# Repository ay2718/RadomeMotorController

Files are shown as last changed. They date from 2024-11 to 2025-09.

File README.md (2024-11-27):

# Radome motor controller

## CAN protocol

The Radome CAN protocol is very simple.  Send azimuth commands to address 0x1 and elevation commands to address 0x2.  Azimuth and elevation reply back from addresses 0x101 and 0x102 respectively.  Any packet sent to address 0x0 will trigger both azimuth and elevation to reply back with their current status without initiating a motor movement, sending commands will also trigger a reply back.

Even if you feed the CAN total garbage the dish will not exceed safe positions (for elevation), speeds, or acceleration.

The controllers must be updated at least every 100 ms or faster. Othewise they will safely bring the dish to a halt.

The command structure is as follows:

```
Transmit:
// 2^24 is 360 degrees, position is unsigned
tx byte 0 = position bits 23:16
tx byte 1 = position bits 15:8
tx byte 2 = position bits 7:0

// LSB is 1 arcsecond/s = 1/1200 dps, signed
tx byte 3 = velocity bits 15:8
tx byte 4 = velocity bits 7:0

Receive:
// 2^24 is 360 degrees, position is unsigned
rx byte 0 = position bits 23:16
rx byte 1 = position bits 15:8
rx byte 2 = position bits 7:0

// LSB is 1 arcsecond/s = 1/1200 dps, signed
rx byte 3 = velocity bits 15:8
rx byte 4 = velocity bits 7:0

// LSB is 1 mA, signed
rx byte 5 = current bits 15:8
rx byte 6 = current bits 7:0

// LSB is 0.5V, unsigned
rx byte 7 = bus voltage bits 7:0
```

I recommend casting position as a `uint32_t` such that 2<sup>32</sup> is equivalent to 360 degrees.  This makes position math very nice since overflow lines up with one rotation.

We feed the dish position *and* velocity because the velocity information in order to generate very smooth trajectories.  If you want to command a position and you don't care much about timing, it's fine to send a position command with zero velocity.  If you're tracking a satellite moving a couple degrees per second across the sky on X band, the velocity really helps (empirically we were able to maintain 0.05 degrees of tracking error up to 10 dps or so)

## Firmware overview

If you decide to build the firmware, this is an STM32CubeIDE project.  You may need to enable floating point support for printf.  Define or underine azimuth or elevation in Core/Inc/main.h to set azimuth or elevation.  Encoder offsets are hardcoded in.

## CAN Bootloader usage

`az_bootloader.bin` and `el_bootloader.bin` should already be loaded onto their respective motor drives.  The bootloader takes up 2 flash pages on each drive (4 kB)

`flash_motor.py` is used to upload firmware over CAN bus.  The baud rate is 125000 (same as for operating the drives).

Example usage: `./flash_motor.py` --id 0x01  -f radome_azimuth.bin`.
The `--id` flag selects which drive to write toe (0x01 is azimuth, 0x02 is elevation) and the `-f` or `--filename` flag selects the binfile to upload.

If a motor drive is unresponsive to being flashed, try running `./flash_motor.py ...`, leave it running, and cycle power to the motor drives.  This is useful if there's a problem with the firmware--`flash_motor.py` sends out pings to each motor's address every 100ms and the drives wait for pings in bootloader mode for 500ms before starting up.

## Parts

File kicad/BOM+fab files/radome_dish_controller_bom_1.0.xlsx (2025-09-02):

Component | Description | Part | References | Value | Footprint | Quantity Per PCB | Datasheet | LCSC | digikeypn | P/N
1 | Unpolarized capacitor | C | ANACAP201 | 10nF | C_0603_1608Metric | 1 | ~ | C1589 | 1276-1009-1-ND
2 | Unpolarized capacitor | C | C113 C114 C201 C202 C203 C204 C205 C206 C304 C305 C306 C308 C309 C312 C313 | 100nF | C_0603_1608Metric | 15 | ~ | C1591 | 1276-1935-1-ND
3 | Unpolarized capacitor | C | C102 C103 C105 C106 C108 C109 | 10uF | C_2220_5650Metric | 6 | ~ | C153035
4 | Unpolarized capacitor | C | C107 C110 C111 C112 | 10uF | C_1206_3216Metric | 4 | ~ | C13585
5 | Unpolarized capacitor | C | C301 C302 C303 C307 C310 C311 | 1uF | C_0603_1608Metric | 6 | ~ | C15849 | 1276-1860-1-ND
6 | Polarized capacitor, US symbol | C_Polarized_US | C101 C104 | 220uF | CP_Radial_D12.5mm_P5.00mm | 2 | ~
7 | 75V 0.15A Fast Switching Diode, SOD-123 | 1N4148W | D301 D302 D303 | 1N4148W | D_SOD-123 | 3 | https://www.vishay.com/docs/85748/1n4148w.pdf | C112342 | 1N4148W-13FDICT-ND
8 | Ferrite bead | FerriteBead | FB201 | 600ohm@100MHz | L_0603_1608Metric | 1 | ~ | C20345 | 732-1593-1-ND
9 | Generic connector, double row, 02x07, odd/even pin numbering scheme (row 1 odd numbers, row 2 even numbers), script generated (kicad-library-utils/schlib/autogen/connector/) | Conn_02x07_Odd_Even | J201 | Conn_02x07_Odd_Even | PinHeader_2x07_P1.27mm_Vertical_SMD | 1 | ~ | C5445007 | 1175-1736-ND
10 | Generic connector, double row, 02x03, top/bottom pin numbering scheme (row 1: 1...pins_per_row, row2: pins_per_row+1 ... num_pins), script generated (kicad-library-utils/schlib/autogen/connector/) | Conn_02x03_Top_Bottom | J106 | Molex Micro-Fit+ | MOLEX_2068320602 | 1 | ~
11 | Generic connector, single row, 01x02, script generated (kicad-library-utils/schlib/autogen/connector/) | Conn_01x02 | J107 J108 | Molex Micro-Fit+ | MOLEX_2165711002 | 2 | ~
12 | Generic screw terminal, single row, 01x01, script generated (kicad-library-utils/schlib/autogen/connector/) | Screw_Terminal_01x01 | J101 J102 J103 J104 J105 | Solder Pad | SolderWirePad_1x01_SMD_5x10mm | 5 | ~
13 | Inductor | L | L101 | 2.2uH | L_Vishay_IHLP-5050 | 1 | https://www.vishay.com/docs/34337/ihlp5050fd5a.pdf | C845090 |  | IHLP5050FDER2R2M5A
14 | 30A Id, 30V Vds, 2.4mOhm Ron, PowerPAK-8 | Si7336ADP | Q301 Q302 Q303 Q304 Q305 Q306 | SIR680DP-T1-RE3 | PowerPAK_SO-8_Single | 6 | https://www.vishay.com/docs/65162/sir426dp.pdf |  | SIR426DP-T1-GE3CT-ND
15 | Resistor | R | R101 | 1 | R_2512_6332Metric | 1 | ~ | C11254
16 | Resistor | R | R204 | 100k | R_0603_1608Metric | 1 | ~ | C25803
17 | Resistor | R | R313 | 10k | R_0603_1608Metric | 1 | ~ | C859110 | RMCF0603FT10K0CT-ND
18 | Resistor | R | R310 R311 | 1k | R_0603_1608Metric | 2 | ~ | C2924142 | RMCF0603FT10K0CT-ND
19 | Shunt resistor | R_Shunt | R307 R308 R309 | 1m | R_Shunt_Vishay_WSK2512_6332Metric_T2.21mm | 3 | ~ | C459678
20 | Resistor | R | R312 | 200k | R_0603_1608Metric | 1 | ~ | C25811 | CR0603-FX-5102ELFCT-ND
21 | Resistor | R | R301 R302 R303 R304 R305 R306 | 3 | R_0603_1608Metric | 6 | ~ | C137724 | RMCF0603FT3R00CT-ND
22 | On-Axis Magnetic Position Sensor, 14-bit, PWM Output, ABI Output, UVW Output, SPI Interface, TSSOP-14 | AS5047D | U101 | AS5047D | TSSOP-14_4.4x5mm_P0.65mm | 1 | https://ams.com/documents/20143/36005/AS5047D_DS000394_2-00.pdf | C962063
23 | 1A 20V Fixed LDO Linear Regulator, 3.3V, SOT-89/SOT-223/TO-220/TO-252/TO-263 | AZ1117-3.3 | U104 | AZ1117-3.3 | SOT-223-3_TabPin2 | 1 | https://www.diodes.com/assets/Datasheets/AZ1117.pdf | C435835
24 | 1A 20V Fixed LDO Linear Regulator, 5.0V, SOT-89/SOT-223/TO-220/TO-252/TO-263 | AZ1117-5.0 | U105 | AZ1117-5.0 | SOT-223-3_TabPin2 | 1 | https://www.diodes.com/assets/Datasheets/AZ1117.pdf | C526405
25 | Bidirectional, Low- and High-Side Voltage Output, Current-Sense Amplifier, SOT-23-6 | INA181 | U304 U305 U306 | INA181-A2 | SOT-23-6 | 3 | http://www.ti.com/lit/ds/symlink/ina181.pdf | C116200 | 296-47657-1-ND
26 | DC/DC buck converter | K78UXX | U106 | K78UXX | K78UXX-RightAngle | 1 | https://www.mornsun-power.com/html/pdf/K78U12-500R3L.html
27 | High and Low Side Driver, 600V, 1.4/1.8A, PDIP-8/SOIC-8 | IRS2181 | U301 U302 U303 | LF2190N | SOIC-8_3.9x4.9mm_P1.27mm | 3 | https://www.littelfuse.com/~/media/electronics/datasheets/power_semiconductors/littelfuse_gate_drivers_lf2190n_datasheet.pdf.pdf | C3655431 | 212-LF2190NTRCT-ND
28 | High-Speed CAN Transceiver, 1Mbps, 3.3V supply | MAX3051 | U202 | MAX3051 | SO-8_3.9x4.9mm_P1.27mm | 1 | http://datasheets.maximintegrated.com/en/ds/MAX3051.pdf | C15648
29 | Differential RS-422/RS-485 bus transceiver, SOIC-8 | SN75176AD | U102 U103 | SN75176AD | SOIC-8_3.9x4.9mm_P1.27mm | 2 | http://www.ti.com/lit/ds/symlink/sn75176a.pdf | C468242
30 |  | STM32G431CBU3_1 | U201 | STM32G431CBU3 | QFN-48-1EP_7x7mm_P0.5mm_EP5.3x5.3mm | 1 |  | C529356 | STM32G431CBU3-ND
31 | Three pin crystal, GND on pin 2 | Crystal_GND2 | Y201 | 16MHz | Resonator_SMD_Murata_CSTxExxV-3Pin_3.0x1.1mm | 1 | ~ | C341521 | 490-17948-1-ND
Component Groups: | 31
Component Count: | 84
Fitted Components: | 84
Number of PCBs: | 1
Total components: | 84
Schematic Version: | 1.0
Schematic Date: | 2023-03-29
BoM Date: | Sat 01 Jul 2023 03:16:00 PM EDT
Schematic Source: | radome_dish_controller.kicad_sch
KiCad Version: | Eeschema 7.0.5-1.fc38

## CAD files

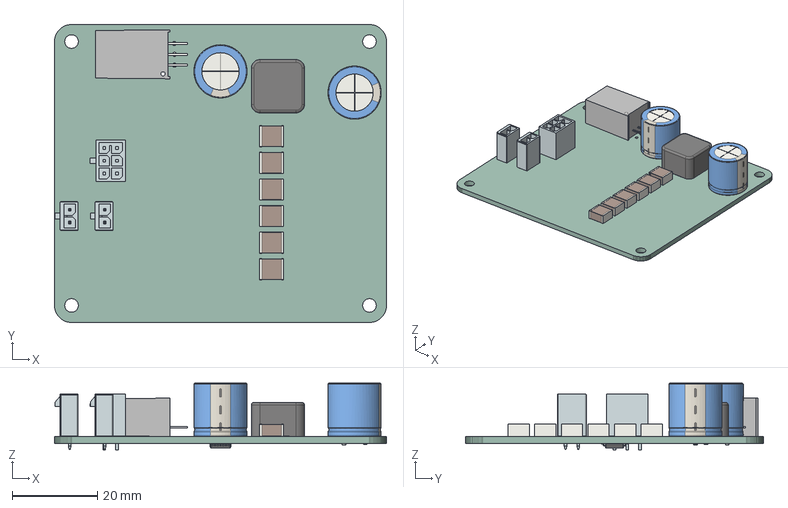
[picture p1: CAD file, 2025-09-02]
kicad/radome_dish_controller.step
78.0 x 70.0 x 15.6 mm
radome_dish_controller PCB

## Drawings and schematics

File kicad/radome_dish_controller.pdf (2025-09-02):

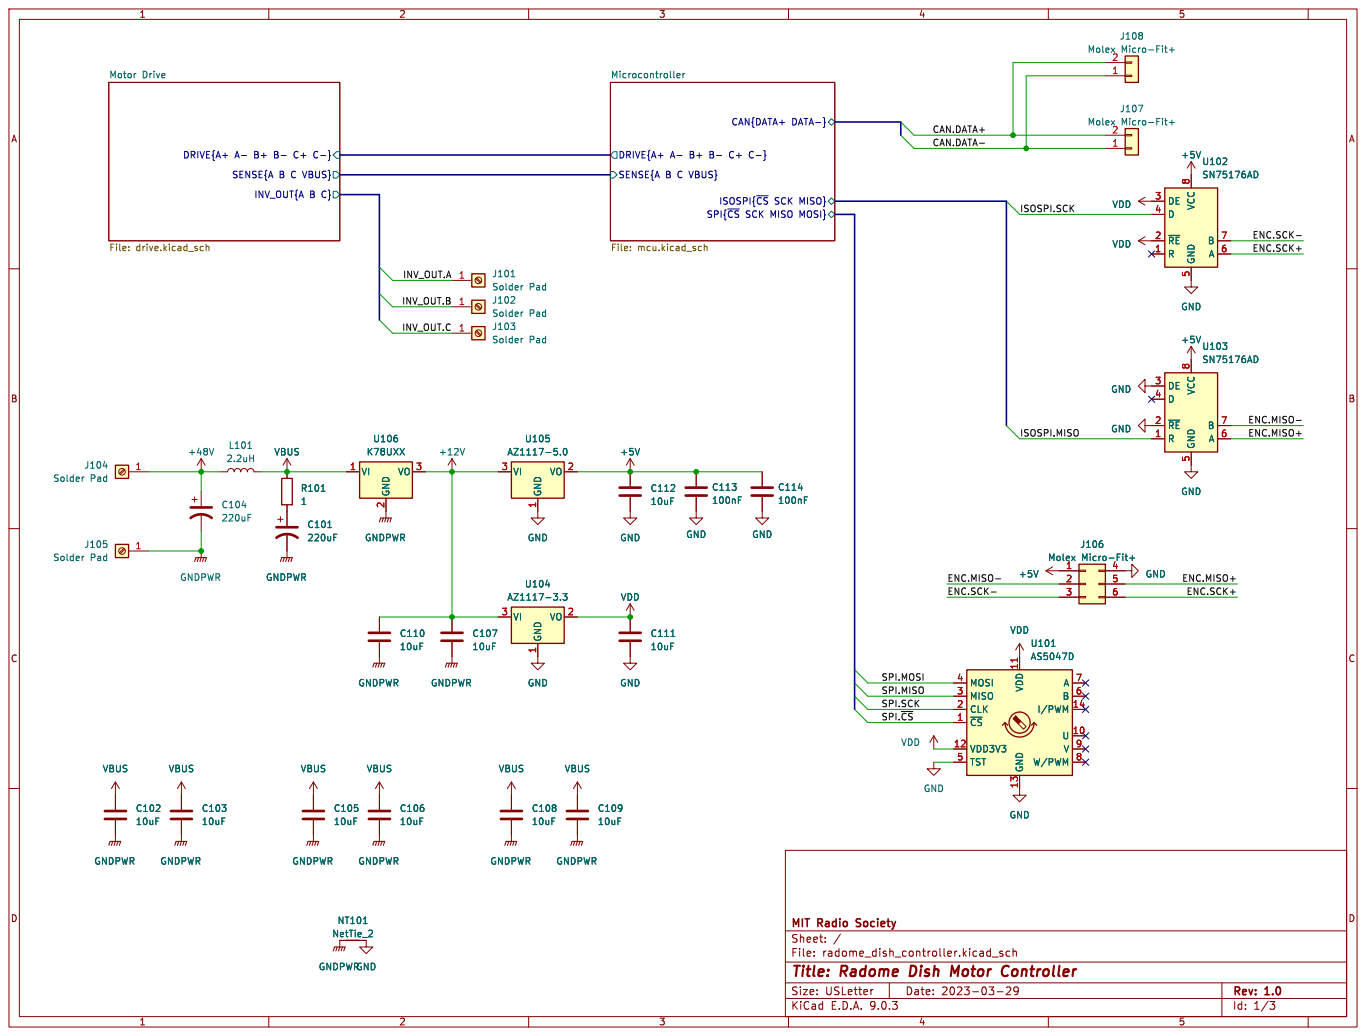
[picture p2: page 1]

SPI{~{CS}SCK MISO MOSI} Microcontroller File: mcu.kicad_sch DRIVE{A+ A- B+ B- C+ C-}

J107 Molex Micro-Fit+ GNDPWR GNDPWR

ISOSPI{~{CS}SCK MISO}

ENC.SCK- SPI.~{CS}

ENC.SCK- ENC.MISO-

SPI.MOSI SPI.MISO

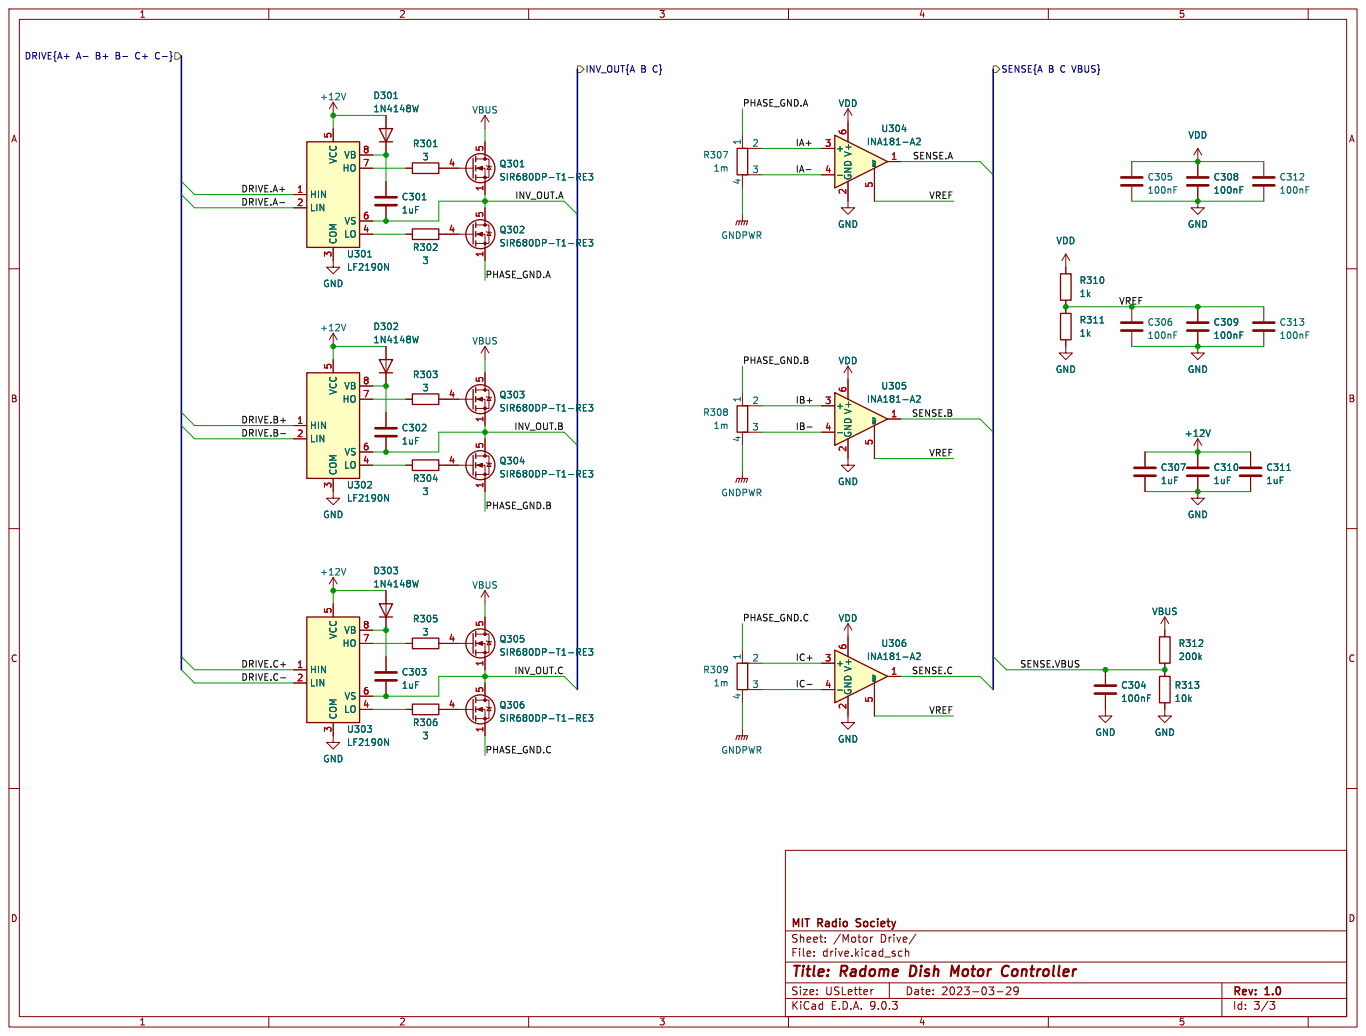
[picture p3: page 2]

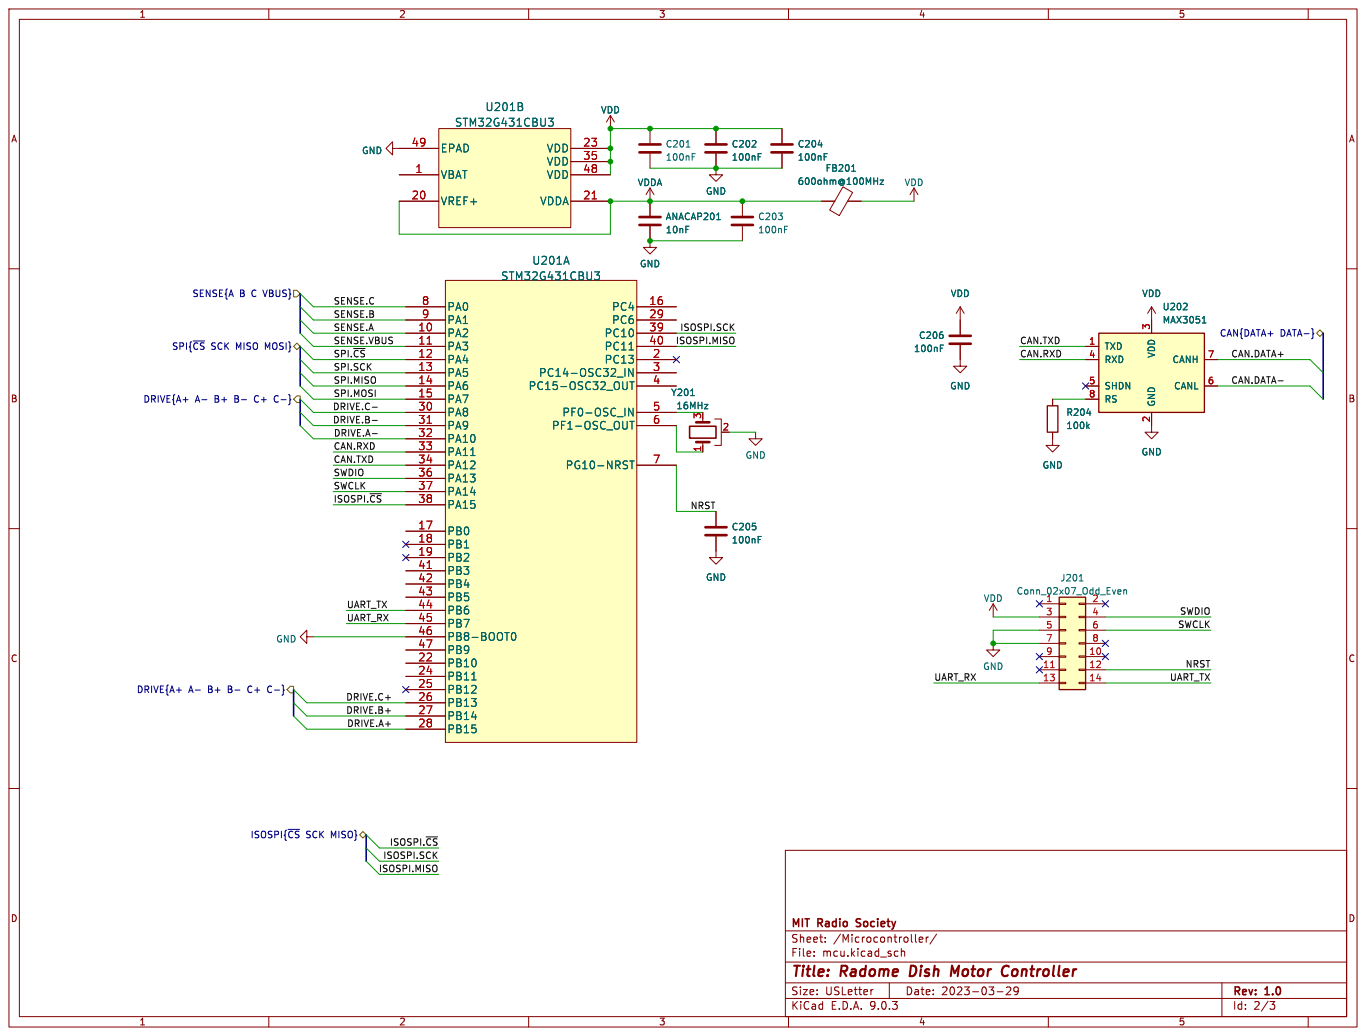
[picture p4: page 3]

SPI.~{CS} SPI.SCK DRIVE.C- DRIVE.B- SENSE.A
SENSE.VBUS

SPI{~{CS}SCK MISO MOSI}

SPI.MOSI SPI.MISO

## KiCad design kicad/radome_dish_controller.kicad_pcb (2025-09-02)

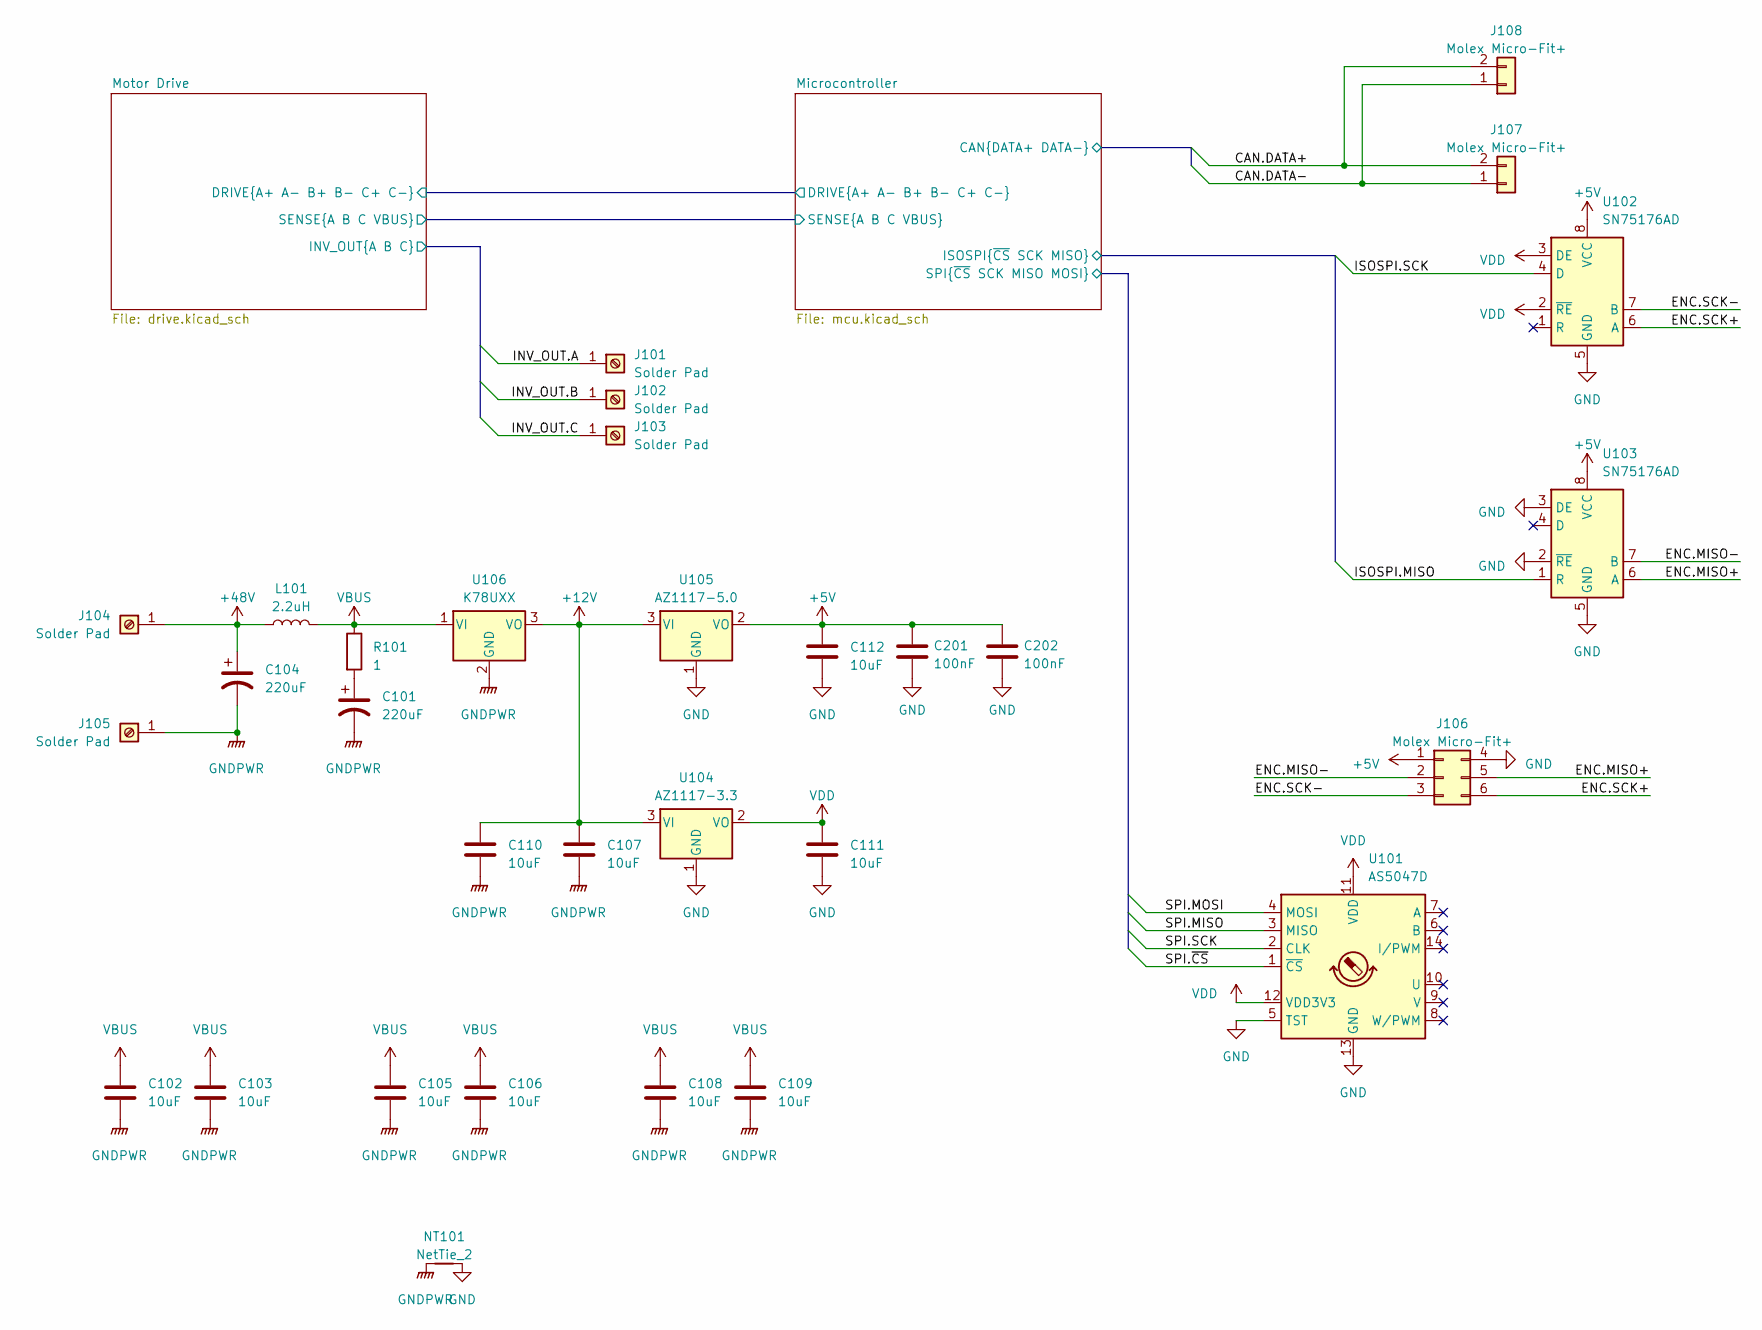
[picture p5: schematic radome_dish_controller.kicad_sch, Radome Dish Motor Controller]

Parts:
C101, C104: 220uF; CP_Radial_D12.5mm_P5.00mm
C102, C103, C105, C106, C108, C109: 10uF; C_2220_5650Metric; LCSC C153035
C107, C110, C111, C112: 10uF; C_1206_3216Metric; LCSC C13585
C201, C202: 100nF; C_0603_1608Metric; digikeypn 1276-1935-1-ND
J101, J102, J103, J104, J105: Solder Pad; SolderWirePad_1x01_SMD_5x10mm
J106: Molex Micro-Fit+; MOLEX_2068320602
J107, J108: Molex Micro-Fit+; MOLEX_2165711002
L101: 2.2uH; L_Vishay_IHLP-5050; LCSC C845090
NT101: NetTie_2; NetTie-2_SMD_Pad2.0mm
R101: 1; R_2512_6332Metric; LCSC C11254
U101: AS5047D; TSSOP-14_4.4x5mm_P0.65mm; LCSC C962063
U102, U103: SN75176AD; SOIC-8_3.9x4.9mm_P1.27mm; LCSC C468242
U104: AZ1117-3.3; SOT-223-3_TabPin2; LCSC C435835
U105: AZ1117-5.0; SOT-223-3_TabPin2; LCSC C526405
U106: K78UXX; K78UXX-RightAngle

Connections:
+12V: C107.1, C110.1, U104.3 (VI), U105.3 (VI), U106.3 (VO); also elsewhere on the board
+48V: C104.1, J104.1, L101.1
/ENC.MISO+: J106.5, U103.6 (A)
/ENC.MISO-: J106.2, U103.7 (B)
/ENC.SCK+: J106.6, U102.6 (A)
/ENC.SCK-: J106.3, U102.7 (B)
/Microcontroller/CAN.DATA+: J107.2, J108.2; also elsewhere on the board
/Microcontroller/CAN.DATA-: J107.1, J108.1; also elsewhere on the board
/Microcontroller/ISOSPI.MISO: U103.1 (R); also elsewhere on the board
/Microcontroller/ISOSPI.SCK: U102.4 (D); also elsewhere on the board
/Microcontroller/SPI.MISO: U101.3 (MISO); also elsewhere on the board
/Microcontroller/SPI.MOSI: U101.4 (MOSI); also elsewhere on the board
/Microcontroller/SPI.SCK: U101.2 (CLK); also elsewhere on the board
/Microcontroller/SPI.~CS: U101.1 (~CS); also elsewhere on the board
/Motor Drive/INV_OUT.A: J101.1; also elsewhere on the board
/Motor Drive/INV_OUT.B: J102.1; also elsewhere on the board
/Motor Drive/INV_OUT.C: J103.1; also elsewhere on the board
GND: C111.2, C112.2, C201.2, C202.2, J106.4, NT101.2, U101.5 (TST), U101.13 (GND), U102.5 (GND), U103.2 (~RE), U103.3 (DE), U103.5 (GND), U104.1 (GND), U105.1 (GND); also elsewhere on the board
GNDPWR: C101.2, C102.2, C103.2, C104.2, C105.2, C106.2, C107.2, C108.2, C109.2, C110.2, J105.1, NT101.1, U106.2 (GND); also elsewhere on the board
unnamed: C101.1, R101.2
VBUS: C102.1, C103.1, C105.1, C106.1, C108.1, C109.1, L101.2, R101.1, U106.1 (VI); also elsewhere on the board

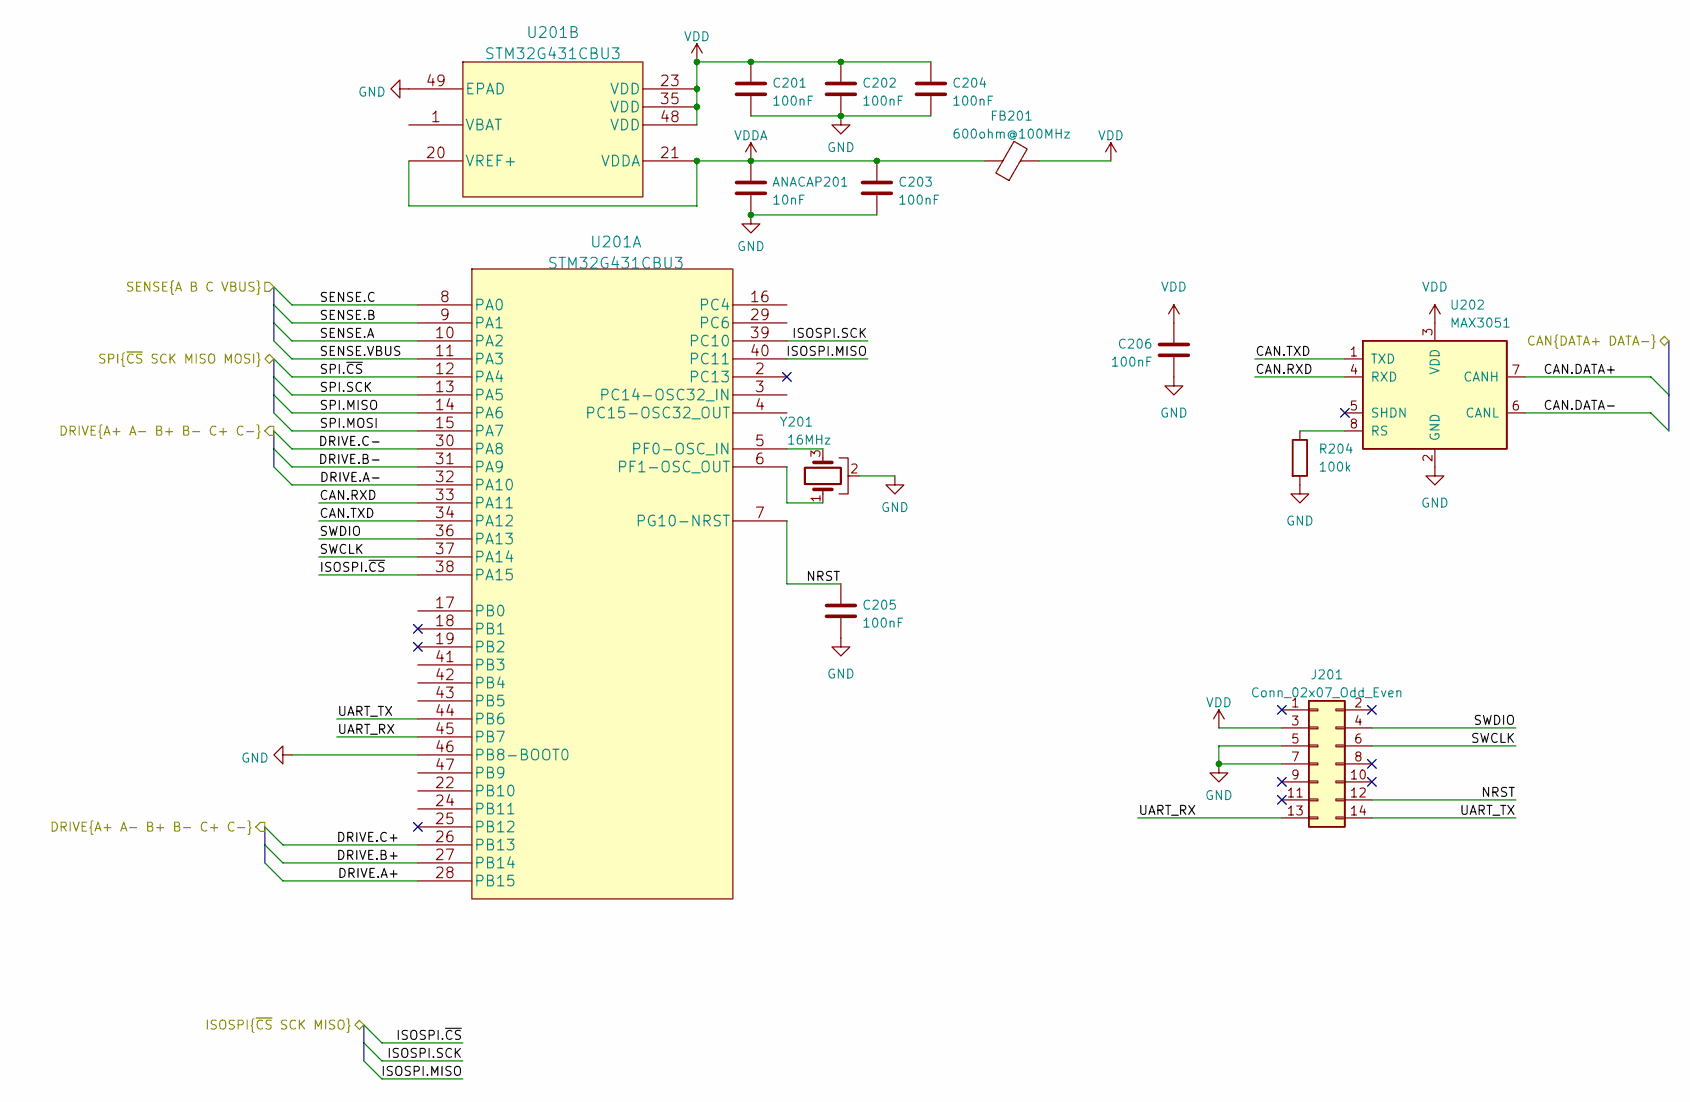
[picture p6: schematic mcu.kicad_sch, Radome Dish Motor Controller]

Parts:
ANACAP201: 10nF; C_0603_1608Metric; digikeypn 1276-1009-1-ND
C201, C202, C203, C204, C205, C206: 100nF; C_0603_1608Metric; digikeypn 1276-1935-1-ND
FB201: 600ohm@100MHz; L_0603_1608Metric; digikeypn 732-1593-1-ND
J201: Conn_02x07_Odd_Even; PinHeader_2x07_P1.27mm_Vertical_SMD; digikeypn 1175-1736-ND
R204: 100k; R_0603_1608Metric; LCSC C25803
U201: STM32G431CBU3; QFN-48-1EP_7x7mm_P0.5mm_EP5.3x5.3mm; digikeypn STM32G431CBU3-ND
U202: MAX3051; SO-8_3.9x4.9mm_P1.27mm; LCSC C15648
Y201: 16MHz; Resonator_SMD_Murata_CSTxExxV-3Pin_3.0x1.1mm; digikeypn 490-17948-1-ND

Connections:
/Microcontroller/CAN.DATA+: U202.7 (CANH); also elsewhere on the board
/Microcontroller/CAN.DATA-: U202.6 (CANL); also elsewhere on the board
/Microcontroller/CAN.RXD: U201.33 (PA11), U202.4 (RXD)
/Microcontroller/CAN.TXD: U201.34 (PA12), U202.1 (TXD)
/Microcontroller/DRIVE.A+: U201.28 (PB15); also elsewhere on the board
/Microcontroller/DRIVE.A-: U201.32 (PA10); also elsewhere on the board
/Microcontroller/DRIVE.B+: U201.27 (PB14); also elsewhere on the board
/Microcontroller/DRIVE.B-: U201.31 (PA9); also elsewhere on the board
/Microcontroller/DRIVE.C+: U201.26 (PB13); also elsewhere on the board
/Microcontroller/DRIVE.C-: U201.30 (PA8); also elsewhere on the board
/Microcontroller/ISOSPI.MISO: U201.40 (PC11); also elsewhere on the board
/Microcontroller/ISOSPI.SCK: U201.39 (PC10); also elsewhere on the board
/Microcontroller/ISOSPI.~CS: U201.38 (PA15)
/Microcontroller/NRST: C205.1, J201.12, U201.7 (PG10-NRST)
/Microcontroller/SENSE.A: U201.10 (PA2); also elsewhere on the board
/Microcontroller/SENSE.B: U201.9 (PA1); also elsewhere on the board
/Microcontroller/SENSE.C: U201.8 (PA0); also elsewhere on the board
/Microcontroller/SENSE.VBUS: U201.11 (PA3); also elsewhere on the board
/Microcontroller/SPI.MISO: U201.14 (PA6); also elsewhere on the board
/Microcontroller/SPI.MOSI: U201.15 (PA7); also elsewhere on the board
/Microcontroller/SPI.SCK: U201.13 (PA5); also elsewhere on the board
/Microcontroller/SPI.~CS: U201.12 (PA4); also elsewhere on the board
/Microcontroller/SWCLK: J201.6, U201.37 (PA14)
/Microcontroller/SWDIO: J201.4, U201.36 (PA13)
/Microcontroller/UART_RX: J201.13, U201.45 (PB7)
/Microcontroller/UART_TX: J201.14, U201.44 (PB6)
GND: ANACAP201.2, C201.2, C202.2, C203.2, C204.2, C205.2, C206.2, J201.5, J201.7, R204.2, U201.46 (PB8-BOOT0), U201.49 (EPAD), U202.2 (GND), Y201.2; also elsewhere on the board
unnamed: U201.5 (PF0-OSC_IN), Y201.3
unnamed: U201.6 (PF1-OSC_OUT), Y201.1
unnamed: R204.1, U202.8 (RS)
VDDA: ANACAP201.1, C203.1, FB201.1, U201.20 (VREF+), U201.21 (VDDA)

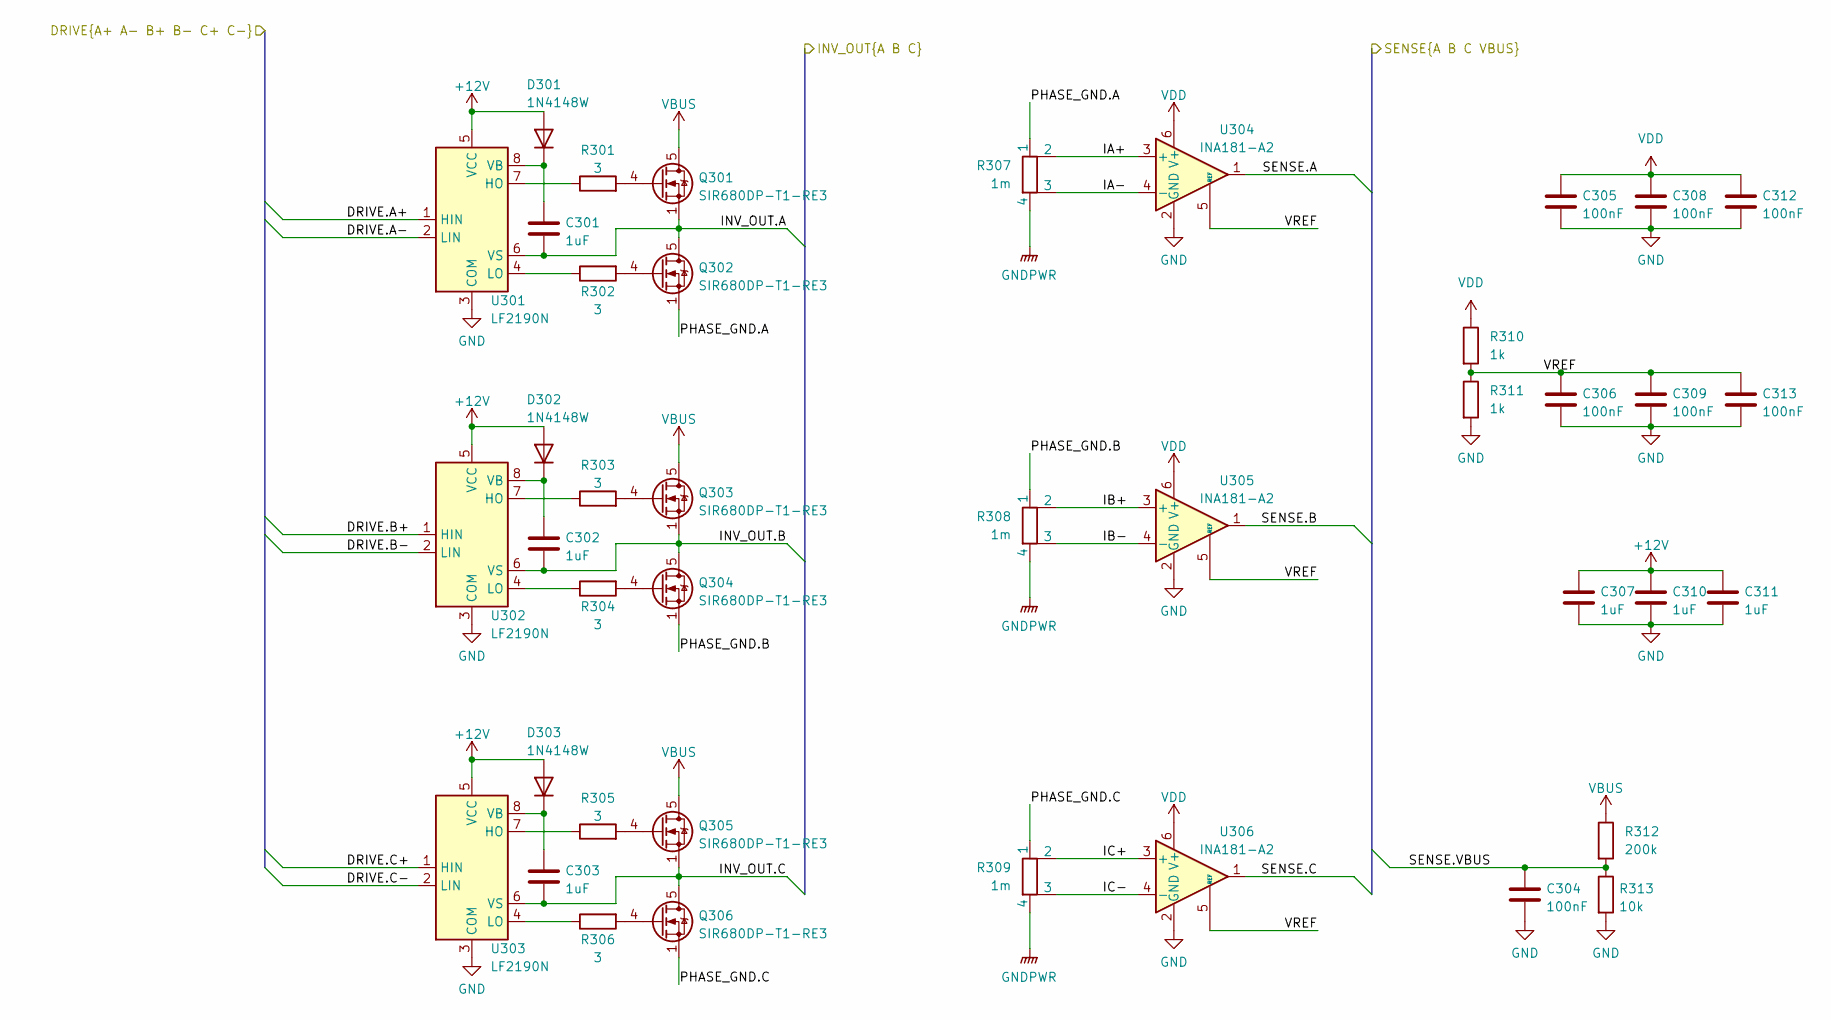
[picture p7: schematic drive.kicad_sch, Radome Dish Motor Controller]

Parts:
C301, C302, C303, C307, C310, C311: 1uF; C_0603_1608Metric; digikeypn 1276-1860-1-ND
C304, C305, C306, C308, C309, C312, C313: 100nF; C_0603_1608Metric; digikeypn 1276-1935-1-ND
D301, D302, D303: 1N4148W; D_SOD-123; digikeypn 1N4148W-13FDICT-ND
Q301, Q302, Q303, Q304, Q305, Q306: SIR680DP-T1-RE3; PowerPAK_SO-8_Single; digikeypn SIR426DP-T1-GE3CT-ND
R301, R302, R303, R304, R305, R306: 3; R_0603_1608Metric; digikeypn RMCF0603FT3R00CT-ND
R307, R308, R309: 1m; R_Shunt_Vishay_WSK2512_6332Metric_T2.21mm; LCSC C459678
R310, R311: 1k; R_0603_1608Metric; digikeypn RMCF0603FT10K0CT-ND
R312: 200k; R_0603_1608Metric; digikeypn CR0603-FX-5102ELFCT-ND
R313: 10k; R_0603_1608Metric; digikeypn RMCF0603FT10K0CT-ND
U301, U302, U303: LF2190N; SOIC-8_3.9x4.9mm_P1.27mm; digikeypn 212-LF2190NTRCT-ND
U304, U305, U306: INA181-A2; SOT-23-6; digikeypn 296-47657-1-ND

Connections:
+12V: C307.1, C310.1, C311.1, D301.2 (A), D302.2 (A), D303.2 (A), U301.5 (VCC), U302.5 (VCC), U303.5 (VCC); also elsewhere on the board
/Microcontroller/DRIVE.A+: U301.1 (HIN); also elsewhere on the board
/Microcontroller/DRIVE.A-: U301.2 (LIN); also elsewhere on the board
/Microcontroller/DRIVE.B+: U302.1 (HIN); also elsewhere on the board
/Microcontroller/DRIVE.B-: U302.2 (LIN); also elsewhere on the board
/Microcontroller/DRIVE.C+: U303.1 (HIN); also elsewhere on the board
/Microcontroller/DRIVE.C-: U303.2 (LIN); also elsewhere on the board
/Microcontroller/SENSE.A: U304.1; also elsewhere on the board
/Microcontroller/SENSE.B: U305.1; also elsewhere on the board
/Microcontroller/SENSE.C: U306.1; also elsewhere on the board
/Microcontroller/SENSE.VBUS: C304.1, R312.2, R313.1; also elsewhere on the board
/Motor Drive/IA+: R307.2, U304.3 (+)
/Motor Drive/IA-: R307.3, U304.4 (-)
/Motor Drive/IB+: R308.2, U305.3 (+)
/Motor Drive/IB-: R308.3, U305.4 (-)
/Motor Drive/IC+: R309.2, U306.3 (+)
/Motor Drive/IC-: R309.3, U306.4 (-)
/Motor Drive/INV_OUT.A: C301.2, Q301.1 (S), Q301.2 (S), Q301.3 (S), Q302.5 (D), U301.6 (VS); also elsewhere on the board
/Motor Drive/INV_OUT.B: C302.2, Q303.1 (S), Q303.2 (S), Q303.3 (S), Q304.5 (D), U302.6 (VS); also elsewhere on the board
/Motor Drive/INV_OUT.C: C303.2, Q305.1 (S), Q305.2 (S), Q305.3 (S), Q306.5 (D), U303.6 (VS); also elsewhere on the board
/Motor Drive/PHASE_GND.A: Q302.1 (S), Q302.2 (S), Q302.3 (S), R307.1
/Motor Drive/PHASE_GND.B: Q304.1 (S), Q304.2 (S), Q304.3 (S), R308.1
/Motor Drive/PHASE_GND.C: Q306.1 (S), Q306.2 (S), Q306.3 (S), R309.1
/Motor Drive/VREF: C306.1, C309.1, C313.1, R310.2, R311.1, U304.5 (REF), U305.5 (REF), U306.5 (REF)
GND: C304.2, C305.2, C306.2, C307.2, C308.2, C309.2, C310.2, C311.2, C312.2, C313.2, R311.2, R313.2, U301.3 (COM), U302.3 (COM), U303.3 (COM), U304.2 (GND), U305.2 (GND), U306.2 (GND); also elsewhere on the board
GNDPWR: R307.4, R308.4, R309.4; also elsewhere on the board
unnamed: C301.1, D301.1 (K), U301.8 (VB)
unnamed: C302.1, D302.1 (K), U302.8 (VB)
unnamed: C303.1, D303.1 (K), U303.8 (VB)
unnamed: Q301.4 (G), R301.2
unnamed: Q302.4 (G), R302.2
unnamed: Q303.4 (G), R303.2
unnamed: Q304.4 (G), R304.2
unnamed: Q305.4 (G), R305.2
unnamed: Q306.4 (G), R306.2
unnamed: R301.1, U301.7 (HO)
unnamed: R302.1, U301.4 (LO)
unnamed: R303.1, U302.7 (HO)
unnamed: R304.1, U302.4 (LO)
unnamed: R305.1, U303.7 (HO)
unnamed: R306.1, U303.4 (LO)
VBUS: Q301.5 (D), Q303.5 (D), Q305.5 (D), R312.1; also elsewhere on the board

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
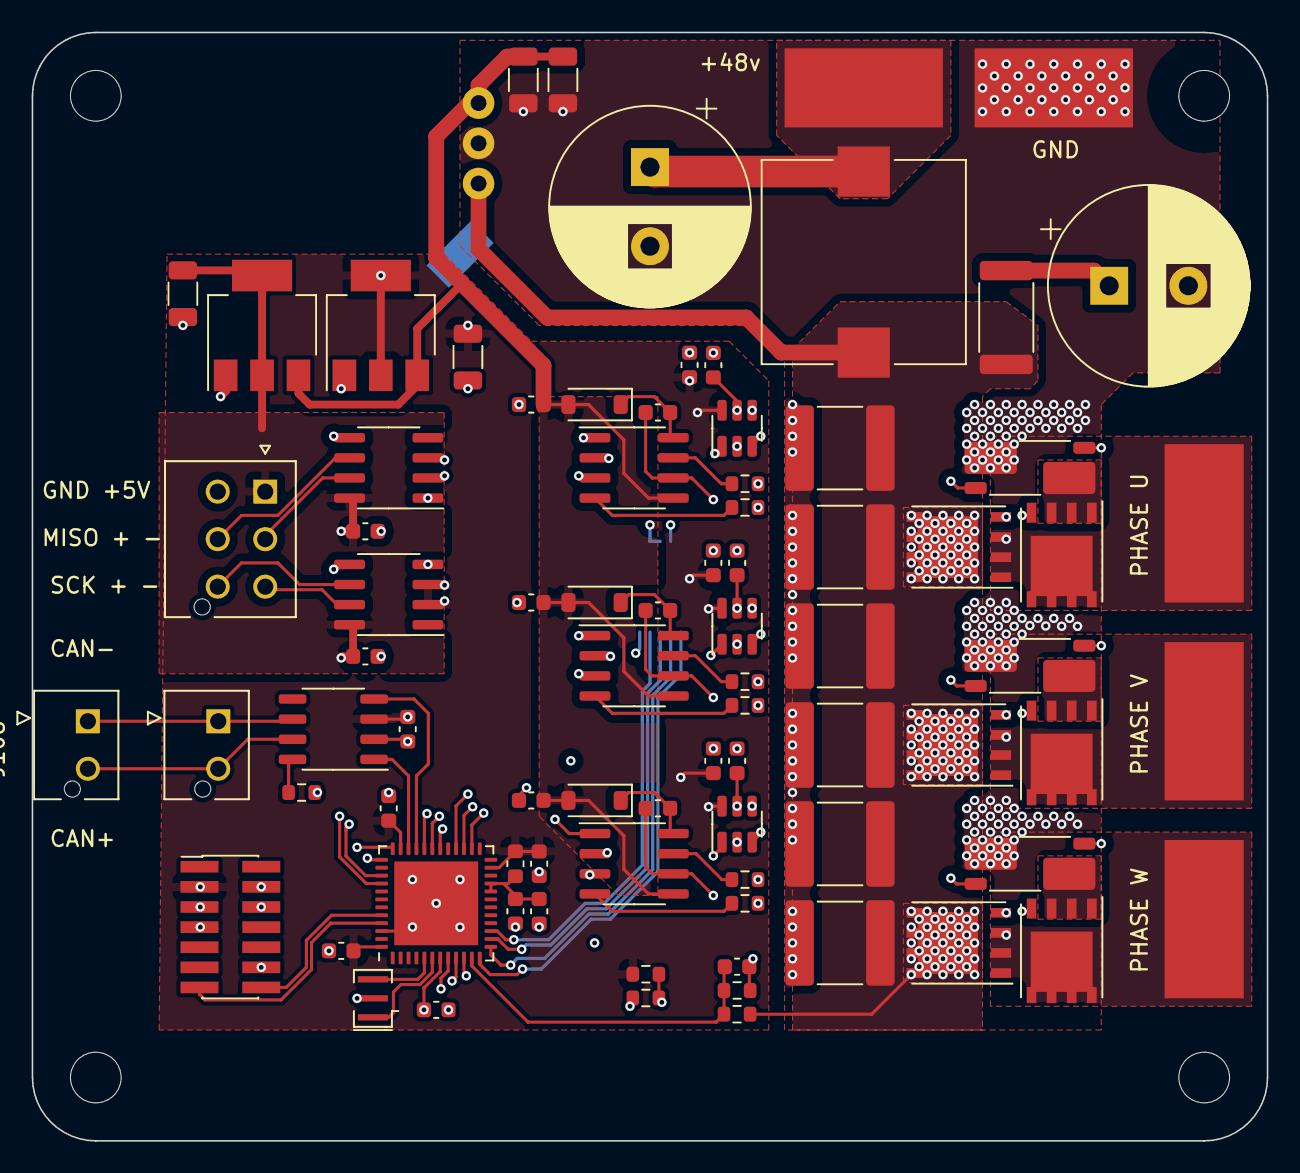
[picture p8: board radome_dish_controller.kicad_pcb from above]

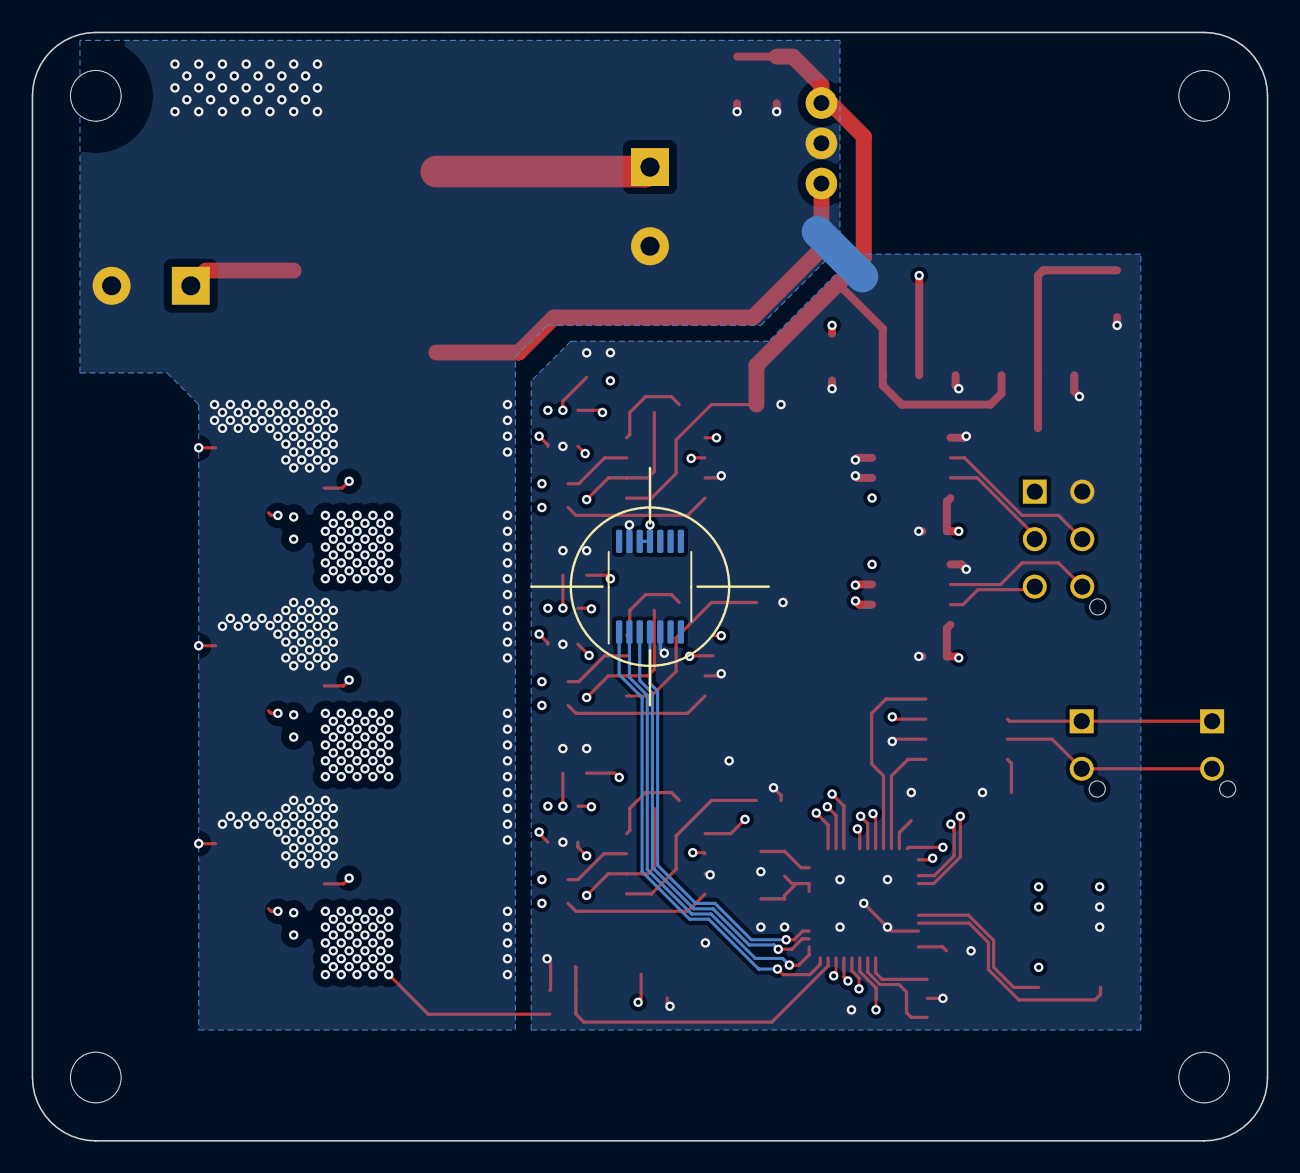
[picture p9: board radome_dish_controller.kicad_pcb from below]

Board: 4 copper layers, 78.0 x 70.0 mm, 85 parts (2 on the bottom side), 69 nets.

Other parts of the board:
C113, C114: 100nF; C_0603_1608Metric

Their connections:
GND: C113.2, C114.2; also elsewhere on the board

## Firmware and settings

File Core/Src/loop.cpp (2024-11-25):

/*
 * control_loop.cpp
 *
 *  Created on: Aug 14, 2022
 *      Author: ayeiser
 */

#include <loop.h>
#include "tim_delay.h"
#include "control.h"
#include "EMFPositionSensor.h"
#include "CurrentSensor.h"
#include "stdio.h"
#include "main.h"
#include "retarget.h"

#include "AS5047PositionSensor.h"
#include "CANHandler.h"
#include "ZettlexIncoder.h"
#include "structs.h"


#define ADC_TO_VOLTAGE (3.3f / 4095.0f)
#define CURRENT_SCALE -(ADC_TO_VOLTAGE / (50.0f * 0.001f)) // 50x shunt gain, 1 mohm shunt
#define VBUS_SCALE (ADC_TO_VOLTAGE * 21.0f) // 200k and 10k divider

#define DELAY_CORR 0.0f

extern TIM_HandleTypeDef htim1, htim6, htim7;
extern ADC_HandleTypeDef hadc1, hadc2;
extern UART_HandleTypeDef huart1;
extern SPI_HandleTypeDef hspi1, hspi3;
extern FDCAN_HandleTypeDef hfdcan1;
extern IWDG_HandleTypeDef hiwdg;

CANHandler canHandler(&hfdcan1);
ZettlexIncoder incoder(&hspi3);

namespace Motor {

#define NUM_POLES 7
const vect_dq Ldq = {250e-6f, 250e-6f};
const float R_phase = 0.3f;

const float dt = 1/float(PWM_FREQ);

ADCReader phaseU(&hadc1, 0, CURRENT_SCALE, 2048);
ADCReader phaseV(&hadc2, 1, CURRENT_SCALE, 2048);
ADCReader phaseW(&hadc2, 0, CURRENT_SCALE, 2048);
ADCReader vbusMeas(&hadc1, 1, VBUS_SCALE, 0);

CurrentSensor current(phaseU, phaseV, phaseW, vbusMeas);
PWMGenerator_WVU pwm(&htim1);
EMFPositionSensor emfpos(current, pwm, dt, NUM_POLES, Ldq, R_phase);
TestPositionSensor fakepos(dt, NUM_POLES);
AS5047PositionSensor as5047pos(&hspi1, dt, NUM_POLES, OFFSET);

LowPassFilter rpmfilter(dt, 100.0f);

CurrentDQController idqc(dt, 10.0f, Ldq, 0.2f);
PIController vel_pi(dt, 0.750f, 0.0f, 0.0f);
//GenericController controller(dt, pos, current, pwm, idqc, DELAY_CORR);

DummyController dummy;
MotorParamFinder params(10.0f);
TorqueController torque(idqc);
//PDVelocityController pdc(idqc, 20.0f);
IncoderPositionController pdc(idqc, incoder, 20.0f);

ParentController* active_controller = &pdc;

motor_command_t motor_command = {
		.position = 0,
		.velocity = 0.0f,
};

motor_reply_t motor_reply = {
		.position = 0,
		.velocity = 0.0f,
		.current = 0.0f,
		.vbus = 0.0f
};

}

const float ParentController::undervoltage_threshold = 15.0f;
const float ParentController::enable_voltage_threshold = 20.0f;
const float ParentController::overvoltage_threshold = 60.0f;
const float ParentController::overcurrent_threshold = 30.0f;

CurrentSensor& ParentController::current = Motor::current;
PWMGenerator& ParentController::pwm = Motor::pwm;
PositionSensor& ParentController::pos = Motor::as5047pos;
//PositionSensor& ParentController::pos = Motor::emfpos;
float ParentController::dt = Motor::dt;

using namespace Motor;


void setup() {
	HAL_Delay(1000);
	RetargetInit(&huart1);
	printf("\n-------------------------------------------------------\n");
	printf(ID_STR "\n");

	printf("Starting CAN...\n");
	canHandler.start();

	printf("Starting ADC reader...\n");
	ADCReader::start();

	printf("Starting htim6...\n");
	start_delay_timer(&htim6);

	printf("Setting up position sensor...\n");
	emfpos.setup();

	as5047pos.setup();

	pdc.setGains(VEL_KP, VEL_KD, PDC_MAX_CURRENT);
	pdc.setPositionGains(0.0f);
	pdc.set_hpf(VEL_HPF);
	pdc.setTargets(as5047pos.getPhaseCorrMechAngle(), 0.0f);
	pdc.setTrajectory(0, 0.0f);


	printf("Setting up PWM generation...\n");
	pwm.startTiming();
	pwm.startSwitching();
	pwm.setAngle(0);
	pwm.update(20.0f);

	HAL_TIM_Base_Start_IT(&htim7);


	printf("Done setup!\n");
}

void loop() {
	// main.c while loop goes here
//	if (active_controller == )

//	if (rxDataReady()) {
//		char c = getchar();
//		printf("c = %c\n", c);
//		if (c == 'x') {
//			ParentController* current = active_controller;
//			active_controller = &params;
//			active_controller->exec();
//			active_controller = current;
//		}
//		if (c == 't') {
//			active_controller = &torque;
//			torque.setTorque(0.0f);
//		}
//		if (c == 'd') {
//			active_controller = &dummy;
//		}
//		if (c == 'p') {
//			active_controller = &pdc;
//			pdc.setGains(100.0f, 0.5f, 10.0f);
//			pdc.setTargets(as5047pos.getPhaseCorrMechAngle(), 0.0f);
//		}
//		if (c == '0') {
//			torque.setTorque(0.0f);
//			pdc.setTargets(0, 0.0f);
//		}
//		if (c == '1') {
//			torque.setTorque(5.0f);
//			pdc.setTargets(0x10000000, 0.0f);
//
//		}
//		if (c == '2') {
//			torque.setTorque(10.0f);
//			pdc.setTargets(0x20000000, 0.0f);
//
//		}
//		if (c == '3') {
//			torque.setTorque(15.0f);
//			pdc.setTargets(0x30000000, 0.0f);
//
//		}
//		if (c == '4') {
//			torque.setTorque(20.0f);
//			pdc.setTargets(0x40000000, 0.0f);
//
//		}
//		if (c == '5') {
//			torque.setTorque(-5.0f);
//			pdc.setTargets(0x50000000, 0.0f);
//
//		}
//		if (c == '6') {
//			torque.setTorque(-10.0f);
//			pdc.setTargets(0x60000000, 0.0f);
//
//		}
//		if (c == '7') {
//			torque.setTorque(-15.0f);
//			pdc.setTargets(0x70000000, 0.0f);
//
//		}
//		if (c == '8') {
//			torque.setTorque(-20.0f);
//			pdc.setTargets(0x80000000, 0.0f);
//
//		}
//		if (c == '9') {
//			torque.setTorque(0.0f);
//			pdc.setTargets(0x90000000, 0.0f);
//
//		}
//
//	}


//	printf("%d 0x%08x    ", incoder.isValid(), incoder.getAngle());
	active_controller->exec();
	HAL_IWDG_Refresh(&hiwdg);

//	uint32_t emf_pos = emfpos.getPhaseCorrElecAngle();
//	uint32_t enc_pos = as5047pos.getPhaseCorrElecAngle();
//	uint32_t diffpos = enc_pos - emf_pos;
//	printf("Positions emf 0x%08x enc 0x%08x diff 0x%08x\n", emf_pos, enc_pos, diffpos);

}

volatile uint32_t invalid_count = 0;

void HAL_TIM_PeriodElapsedCallback(TIM_HandleTypeDef *htim) {
	if (htim->Instance == TIM1) {
//		if (htim->Instance->CR1 & TIM_CR1_DIR) {
//			emfpos.update();
//		}
		if (htim->Instance->CR1 & TIM_CR1_DIR) {
			if (HAL_GetTick() - motor_command.last_tick > 100) {
				pdc.setPositionGains(0.0f);
				pdc.setTrajectory(incoder.getAngle(), 0.0f);
				motor_command.last_tick = HAL_GetTick() - 1000;
			} else {
				if (!incoder.isValid()) {
					invalid_count++;
				} else {
					invalid_count = 0;
				}
				if (invalid_count > 100) {
					invalid_count = 1000;
					motor_command.last_tick = HAL_GetTick() - 1000;
				}
				pdc.setPositionGains(VEL_POS_GAIN);
#ifdef ELEVATION
				pdc.setTrajectory(-motor_command.position, -motor_command.velocity);
#endif

#ifdef AZIMUTH
				pdc.setTrajectory(motor_command.position, motor_command.velocity);
#endif
			}

#ifdef ELEVATION
			motor_reply.position = -incoder.getAngle();
			motor_reply.velocity = -as5047pos.getMechVelocity() / GEAR_REDUCTION;
			motor_reply.current = -ParentController::getCurrents().q;
			motor_reply.vbus = ParentController::getVbus();
#endif

#ifdef AZIMUTH
			motor_reply.position = incoder.getAngle();
			motor_reply.velocity = as5047pos.getMechVelocity() / GEAR_REDUCTION;
			motor_reply.current = ParentController::getCurrents().q;
			motor_reply.vbus = ParentController::getVbus();
#endif
		}
		active_controller->update(htim);
	}

	if (htim->Instance == TIM7) {
		incoder.update();
	}
}

//
void HAL_FDCAN_RxFifo0Callback(FDCAN_HandleTypeDef *hfdcan, uint32_t RxFifo0ITs) {
//	if((RxFifo0ITs & FDCAN_IT_RX_FIFO0_NEW_MESSAGE) != RESET) {
//
//	}
	while(canHandler.popRx(FDCAN_RX_FIFO0) == HAL_OK) {
		canHandler.processRxCAN(&motor_command, &motor_reply);
	}
}

void HAL_FDCAN_RxFifo1Callback(FDCAN_HandleTypeDef *hfdcan, uint32_t RxFifo1ITs) {
	while(canHandler.popRx(FDCAN_RX_FIFO1) == HAL_OK) {
		canHandler.processRxCAN(&motor_command, &motor_reply);
	}
}

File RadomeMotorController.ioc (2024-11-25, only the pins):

Mcu.UserName=STM32G431CBUx
PA0.GPIO_Label=SOC
PA0.Signal=ADC2_IN1
PA1.GPIO_Label=SOB
PA1.Signal=ADC2_IN2
PA10.Signal=S_TIM1_CH3
PA11.Signal=FDCAN1_RX
PA12.Signal=FDCAN1_TX
PA13.Signal=SYS_JTMS-SWDIO
PA14.Signal=SYS_JTCK-SWCLK
PA15.Signal=GPIO_Output
PA2.GPIO_Label=SOA
PA2.Signal=ADC1_IN3
PA3.GPIO_Label=VBUS_SENSE
PA3.Signal=ADC1_IN4
PA4.GPIO_Label=SPI1_CS
PA4.Signal=GPIO_Output
PA5.Signal=SPI1_SCK
PA6.Signal=SPI1_MISO
PA7.Signal=SPI1_MOSI
PA8.Signal=S_TIM1_CH1
PA9.Signal=S_TIM1_CH2
PB13.Signal=TIM1_CH1N
PB14.Signal=TIM1_CH2N
PB15.Signal=TIM1_CH3N
PB6.Signal=USART1_TX
PB7.Signal=USART1_RX
PC10.Signal=SPI3_SCK
PC11.Signal=SPI3_MISO
PF0-OSC_IN.Signal=RCC_OSC_IN
PF1-OSC_OUT.Signal=RCC_OSC_OUT

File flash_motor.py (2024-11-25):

#! /usr/bin/env python3

import can
import os
import time
import struct
import argparse
from ctypes import *
from math import *
from util import *

# Add the following line to /etc/sudoers.d/network_interface
# ALL ALL=(ALL) NOPASSWD: /usr/bin/ip link set can0 *

class bootloader_writer:
    def __init__(self, device_id, bus):
        self.bus = bus
        self.device_id = device_id

        self.PAGE_SIZE = 0x800

        self.CMD_MASK   = 0x01000000
        self.REPLY_MASK = 0x08000000
        self.ERROR_MASK = 0x00800000
        self.BASE_CMD   = 0x10000000 + device_id

    def __del__(self):
        self.bus.shutdown()

    def clear_bus(self):
        while self.bus.recv(0):
            pass
    
    def wait_for_reply(self, cmd, timeout = 1):
        t = time.time()
        while time.time() - t < timeout:
            msg = self.bus.recv(0)
            if msg is None:
                continue

            cmd |= self.REPLY_MASK

            id = msg.arbitration_id

            if id == cmd:
                is_valid = (msg.arbitration_id & self.ERROR_MASK) == 0
                return is_valid, msg
            
        return None
    
    def read_binary_data(self, bindata, position):
        
        length = len(bindata) - position

        if length <= 0:
            return None
        

        if length < 8:
            bytes_littleendian = bindata[position:] + b'\xff' * (8 - length)
        else:
            bytes_littleendian = bindata[position:position + 8]

        # Unpack the data as two little-endian 32-bit unsigned ints
        bytes_bigendian = struct.pack('>II',
                *struct.unpack('<II', bytes_littleendian))

        return bytes_bigendian
    
    def send_cmd(self, cmd, data, timeout = 0.1):
        self.clear_bus()
        while True:
            try:
                self.bus.send(can.Message(arbitration_id=cmd, data=data))
            except:
                pass

            reply = self.wait_for_reply(cmd, timeout)
            if reply is not None:
                return reply
    
    def ping(self):
        cmd = self.BASE_CMD | self.CMD_MASK * 0
        return self.send_cmd(cmd, b'\x00\x00\x00\x00\x00\x00\x00\x00')
    
    def pagesel(self, page):
        page <<= 8
        cmd = self.BASE_CMD | page | self.CMD_MASK * 1
        return self.send_cmd(cmd, b'\x00\x00\x00\x00\x00\x00\x00\x00')
    
    def lock(self):
        cmd = self.BASE_CMD | self.CMD_MASK * 2
        return self.send_cmd(cmd, b'\x00\x00\x00\x00\x00\x00\x00\x00')
    
    def unlock(self):
        cmd = self.BASE_CMD | self.CMD_MASK * 3
        return self.send_cmd(cmd, b'\x00\x00\x00\x00\x00\x00\x00\x00')
    
    def erase(self, page):
        page <<= 8
        cmd = self.BASE_CMD | page | self.CMD_MASK * 4
        return self.send_cmd(cmd, b'\x00\x00\x00\x00\x00\x00\x00\x00')
    
    def write(self, addr, data):
        addr = (addr % self.PAGE_SIZE) << 5
        cmd = self.BASE_CMD | addr | self.CMD_MASK * 5
        return self.send_cmd(cmd, data)
    
    def read(self, addr):
        addr = (addr % self.PAGE_SIZE) << 5
        cmd = self.BASE_CMD | addr | self.CMD_MASK * 6
        return self.send_cmd(cmd, b'\x00\x00\x00\x00\x00\x00\x00\x00')
    
    def finish(self):
        cmd = self.BASE_CMD | self.CMD_MASK * 7
        return self.send_cmd(cmd, b'\x00\x00\x00\x00\x00\x00\x00\x00')
    
    def write_file(self, bindata, page_offset):
        print(f'Pinging device 0x{self.device_id:02x}...')
        self.ping()
        if not self.unlock()[0]:
            print(f'Failed to unlock device 0x{self.device_id:02x}')
            return False
        
        page = page_offset - 1
        position = 0

        while True:
            data = self.read_binary_data(bindata, position)

            if data is None:
                break

            newpage = (position // self.PAGE_SIZE) + page_offset
            if (newpage != page):
                page = newpage
                print(f'Writing page {page:3d} to device 0x{self.device_id:02x}...')
                if not self.pagesel(page)[0]:
                    print(f'Failed to select page {page:3d}')
                    return False

                if not self.erase(page)[0]:
                    print(f'Failed to erase page {page:3d}')
                    return False

            ret, msg = self.write(position, data)
            if not ret or msg.data != data:
                realpos = position + page_offset * self.PAGE_SIZE
                print(f'Failed to write data at position {realpos}')
                return False
            
            position += 8

        
        if not self.lock()[0]:
            print(f'Failed to lock device 0x{self.device_id:02x}')
            return False
        
        if not self.finish()[0]:
            print(f'Failed to finish writing')
            return False
        
        print(f'Finished writing to device 0x{self.device_id:02x}')

def main():
    parser = argparse.ArgumentParser(description='Upload a binary file to a bootloader')
    parser.add_argument('--id', type=int_base_auto, default = 0xff, help='The device ID to upload to')
    parser.add_argument('--filename', '-f', type=str, help='The binary file to upload')
    parser.add_argument('--bootloader', '-b', type=str, default='bootloader.bin', help='The bootloader file to upload')
    parser.add_argument('--page_offset', type=int, default=2, help='The page offset to use')
    parser.add_argument('--last-page', type=int, default=63, help='The last page in flash')
    parser.add_argument('--dev', type=str, default='can0', help='The CAN device to use')
    parser.add_argument('--bitrate', type=int, default=125000, help='The CAN bitrate to use')
    parser.add_argument('--stlink', action='store_true', help='Use ST-Link to program')
    parser.add_argument('--erase', '-e', action='store_true', help='Erase the flash before programming')

    args = parser.parse_args()

    if args.stlink:
        if args.erase:
            os.system(f'st-flash erase')
            os.system(f'st-flash write {args.bootloader} 0x08000000')
            os.system(f'st-flash write {args.filename} 0x08001000')
        os.system(f'st-flash reset')
        return


    bus = get_can_adapter(args.dev, args.bitrate)

    writer = bootloader_writer(args.id, bus)

    if args.filename:
        with open(args.filename, 'rb') as f:
            bindata = f.read()

        writer.write_file(bindata, args.page_offset)

    print('Finished programming!')

if __name__ == '__main__':
    main()

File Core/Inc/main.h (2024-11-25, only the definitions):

#define ID_STR "AZIMUTH"
#define OFFSET 0x90000000
#define ID 1
#define VEL_FUDGE_FACTOR 1.04f
#define GEAR_REDUCTION 472.0f
#define VEL_KP 30.0f
#define VEL_HPF 10.0f
#define VEL_KD 0.3f
#define VEL_POS_GAIN 2.0f
#define PDC_MAX_CURRENT 10.0f
#define ID_STR "ELEVATION"
#define OFFSET 0xa2000000
#define ID 2
#define VEL_FUDGE_FACTOR 1.04f
#define GEAR_REDUCTION 1078.21f
#define VEL_KP 30.0f
#define VEL_HPF 10.0f
#define VEL_KD 0.3f
#define VEL_POS_GAIN 1.0f
#define PDC_MAX_CURRENT 15.0f
#define EL_UPPER_HARDSTOP uint32_t(int32_t(0x1p32f * 2.0f / 360.0f)) // note that elevation is REVERSED!!!
#define EL_LOWER_HARDSTOP uint32_t(int32_t(0x1p32f * -87.0f / 360.0f))
#define MAX_MOTOR_SLEW 40.0f
#define MAX_MOTOR_VELOCITY 200.0f
#define VELOCITY_LSB ((3.0f * PI) / (3600.0f * 180.0f)) // 3 arcseconds/s, max speed is about 27 dps, earth rotation is 5 LSB
#define CURRENT_LSB 0.001f // LSB is 1 mA
#define VBUS_LSB 0.5f
#define ADC_SAMPLES 4
#define CLOCK_FREQ 170000000
#define DEAD_TIME 140
#define ADC_SEQ_LEN 2
#define PWM_ADC_TRIG (ADC_CLK_SCALE * ADC_SEQ_LEN * ADC_SAMPLES / 2)
#define PWM_FREQ 20000
#define ADC_CLK_SCALE (3 * 25)
#define PWM_PERIOD (CLOCK_FREQ / (PWM_FREQ * 2))
#define ADC_SW_OFFSET 180
#define SOC_Pin GPIO_PIN_0
#define SOC_GPIO_Port GPIOA
#define SOB_Pin GPIO_PIN_1
#define SOB_GPIO_Port GPIOA
#define SOA_Pin GPIO_PIN_2
#define SOA_GPIO_Port GPIOA
#define VBUS_SENSE_Pin GPIO_PIN_3
#define VBUS_SENSE_GPIO_Port GPIOA
#define SPI1_CS_Pin GPIO_PIN_4
#define SPI1_CS_GPIO_Port GPIOA

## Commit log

2025-09-02 Added kicad files for radome controller
    [drive.kicad_sch, mcu.kicad_sch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]
2025-09-02 add schematic pdf

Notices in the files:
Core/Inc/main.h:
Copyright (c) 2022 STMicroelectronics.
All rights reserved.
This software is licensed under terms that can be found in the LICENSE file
